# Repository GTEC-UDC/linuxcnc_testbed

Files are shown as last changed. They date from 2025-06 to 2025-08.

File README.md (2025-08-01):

# LinuxCNC Motor Control Testbed

A motor control testbed using the open-source [LinuxCNC](https://www.linuxcnc.org) platform integrated with the [Mesa Electronics](https://store.mesanet.com/) 7i96S and 7I77 interface cards and the [igus® dryve D1](https://www.igus.eu/product/D1) motor controllers.

This system was used to develop and validate the control system for [a large high-precision 3-axis gantry robot system](https://github.com/GTEC-UDC/linuxcnc_gantry_robot).

<div align="center">






</div>

<div align="center">
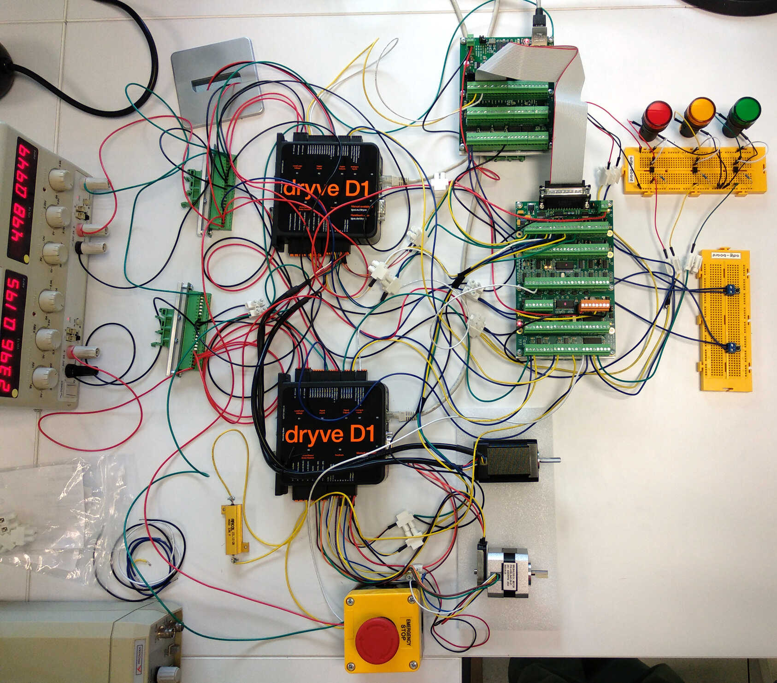
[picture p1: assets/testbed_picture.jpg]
LinuxCNC Motor Control Testbed Picture
  
</div>

<!-- Video uploaded via drag-and-drop to the GitHub editor -->
<!-- Note: GitHub does not render video files from the repository. See: https://github.com/orgs/community/discussions/19403 -->
<!-- The video is also stored at assets/testbed_video.webm within the repo -->
<video type="video/webm" src="https://github.com/user-attachments/assets/f6507526-396f-41c5-9737-cb749e45726b"><video/>

## Key Features

- **Real-time Control**: Precise real-time multi-axis motion using LinuxCNC with MESA interface cards and igus® dryve D1 motor controllers.
- **Dual Motor System**: Stepper and brushless motors.
- **Closed Loop Control**: High-precision encoder feedback for accurate positioning.
- **Safety Systems**: Emergency stop and limit switches.
- **Visual Indicators**: Custom LED status system.

## Documentation

- **Technical Documentation**: [Sphinx](https://www.sphinx-doc.org) documentation sources of the system documentation in [docs/](docs/). The documentation has been prepared to be built in HTML and PDF formats. To build the documentation follow the instructions below:

  1. **Prepare the environment**:

     ```bash
     cd docs
     uv venv && uv sync && source .venv/bin/activate
     ```

  2. **Build the documentation**:

     - HTML: `make html`

       The HTML documentation index file will be saved in `docs/build/html/index.html`.

     - PDF (requires a LaTeX installation with LuaLaTeX): `make latexpdf`

       The PDF file will be saved in `docs/build/latex/linuxcnc_motor_control_testbed.pdf`.

- **Electrical Schematics**: [KiCAD](https://www.kicad.org/) electrical schematics in [schematics/](schematics/).

## Hardware Components

| Component | Model | Quantity | Function |
|---|---|---|---|
| **Control Computer** | PC running [LinuxCNC](https://www.linuxcnc.org) | 1 | Real-time motor coordination |
| **Motor Controllers** | [igus® dryve D1](https://www.igus.eu/product/D1) | 2 | Individual motor control |
| **Main Interface** | [MESA 7I96S](https://store.mesanet.com/index.php?route=product/product&product_id=374) | 1 | Ethernet-LinuxCNC bridge. Stepper motor control. Limits detection |
| **I/O Expansion** | [MESA 7I77](https://store.mesanet.com/index.php?route=product/product&product_id=120) | 1 | Brushless motor control. Encoder inputs. Emergency stop detection and LED indicators|
| **Stepper Motor** | [STEPPERONLINE 17HS24-2104-ME1K](https://www.omc-stepperonline.com/nema-17-closed-loop-stepper-motor-65ncm-92oz-in-with-magnetic-encoder-1000ppr-4000cpr-17hs24-2104-me1k) | 1 | Stepper motor with 1000 PPR magnetic encoder |
| **Brushless Motor** | [STEPPERONLINE 42BLS40-24-01](https://www.omc-stepperonline.com/es/24v-4000rpm-0-0625nm-26w-1-8a-42x42x40mm-motor-cc-sin-escobillas-42bls40-24-01) + [CUI Devices AMT102-0512-I5000-S](https://mou.sr/3GkCI6g) | 1 | Brushless motor with 512 PPR optical encoder |
| **Power Supply** | [Aim-TTI EL302RD](https://www.aimtti.com/product-category/dc-power-supplies/aim-el-rseries) | 1 | Dual output (24V/5V) |
| **Emergency Stop** | Push-button with NO/NC contacts | 1 | System safety shutdown |
| **Limit Switches** | Push-button switches | 2 | Position boundary detection |
| **LED Indicators** | 24 V panel mount LEDs | 3 | System state indication |

## System Architecture

Prototype System

## Repository Structure

```txt
linuxcnc-testbed/
├── README.md      # This file
├── assets/        # Pictures and videos
├── docs/          # Technical Documentation
├── linuxcnc/      # LinuxCNC configurations
├── schematics/    # Wiring diagrams
├── scripts/       # Example control scripts
└── gcode/         # G-code example
```

## License

### General License (unless otherwise specified)

<a rel="license" href="http://creativecommons.org/licenses/by-sa/4.0/">

</a>

[LinuxCNC Motor Control Testbed](https://github.com/GTEC-UDC/linuxcnc_testbed) © 2025 by [Tomás Domínguez Bolaño](https://orcid.org/0000-0001-7470-0315), [Valentín Barral Vales](https://orcid.org/0000-0001-8750-7960), [Carlos José Escudero Cascón](https://orcid.org/0000-0002-3877-1332), and [José Antonio García Naya](https://orcid.org/0000-0002-1944-4678) (CITIC Research Center, University of A Coruña, Spain) is licensed under [Creative Commons Attribution-ShareAlike 4.0 International](https://creativecommons.org/licenses/by-sa/4.0/) (CC BY-SA 4.0). To view a copy of this license, see the [LICENSE-CC](LICENSE-CC) file or visit <https://creativecommons.org/licenses/by-sa/4.0/>.

### Documentation License ([docs/](docs/))

Copyright © 2000-2022 LinuxCNC.org\
Copyright © 2025 Tomás Domínguez Bolaño, Valentín Barral Vales, Carlos José Escudero Cascón, and José Antonio García Naya.

Permission is granted to copy, distribute and/or modify this document
under the terms of the GNU Free Documentation License, Version 1.3
or any later version published by the Free Software Foundation;
with no Invariant Sections, no Front-Cover Texts, and no Back-Cover Texts.
A copy of the license is included in the section entitled "GNU Free Documentation License".

## Acknowledgements

This work has been supported by grant PID2022-137099NB-C42 (MADDIE) and by project TED2021-130240B-I00 (IVRY) funded by MCIN/AEI/10.13039/501100011033 and the European Union NextGenerationEU/PRTR.

<div align="center">
  Acknowledgements logos
</div>

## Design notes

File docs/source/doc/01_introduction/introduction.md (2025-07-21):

# Introduction

The system uses LinuxCNC as its control platform, with two igus® dryve D1 controllers which are used to control a stepper motor and a brushless motor, respectively. The system diagram is shown in {numref}`fig:system_diagram`. Below, we detail the system's configuration, including the boards and components used.

:::{ext-figure} images/system_diagram.\*
:height-html: 300px
:name: fig:system_diagram

System diagram.
:::

## LinuxCNC

LinuxCNC, formerly known as the {{EMC}}, is a software system designed for the computer control of various machine tools, such as milling machines and lathes, as well as robots like PUMA and SCARA, and other computer-controlled machinery with up to nine axes. LinuxCNC is free, open-source software. Current versions are fully licensed under the [{{GPL}}](https://www.gnu.org/licenses/gpl.html) and [{{LGPL}}](https://gnu.org/licenses/lgpl.html).

In our system, LinuxCNC communicates with the igus® dryve D1 controllers via the MESA 7I96S and 7I77 boards. LinuxCNC is responsible for coordinating the operation of all motors, providing precise, real-time control over the system.

Detailed information on LinuxCNC’s operation and configuration can be found in {numref}`sec:linuxcnc`.

## System Hardware

{numref}`fig:installation` shows a photograph of the testbed setup. This system comprises the following key components:

:::{figure} images/installation_labelled.*
:name: fig:installation

Testbed setup.
:::

- **[Aim-TTI EL302RD](https://www.aimtti.com/product-category/dc-power-supplies/aim-el-rseries) Dual Power Supply**: Provides two independent power outputs, each capable of delivering a maximum of 30 V and 2 A. For the testbed setup, we required 24 V and 5 V power.

- **Two [igus® dryve D1](https://www.igus.eu/product/D1) Motor Controllers**: igus® dryve D1 can be used for controlling stepper, DC, and brushless motors in industrial and automation applications. The igus® dryve D1 supports the following communication methods with control systems:

  - **CANopen**: A communication protocol widely used in industrial automation systems, built upon the CAN bus (ISO 11898) standard.
  - **Modbus TCP**: A communication protocol extensively employed in industrial applications for data transmission over Ethernet networks using the TCP protocol.
  - **Analog and Digital Signals**: In addition to network communication options, the igus® dryve D1 can receive analog and digital signals for direct control.

    In this system, we communicate with the igus® dryve D1 controllers using MESA 7I96S and 7I77 boards using digital and analog signals. This setup enables LinuxCNC to have precise, real-time control over the motors' operation.

- **[MESA 7I96S](https://store.mesanet.com/index.php?route=product/product&product_id=374) Board**: This board is the primary hardware interface between LinuxCNC and the igus® dryve D1 controllers. It connects to the computer running LinuxCNC via an Ethernet connection. Its main functions include:

  - Controlling the stepper motor by sending step and direction signals to its designated igus® dryve D1 controller.
  - Receiving input signals from limit switches.

- **[MESA 7I77](https://store.mesanet.com/index.php?route=product/product&product_id=120) Daughter Board**: This board connects to the 7I96S board via a 25-pin flat cable. Its primary functions are:

  - Controlling the brushless motor by sending an analog speed signal to its corresponding igus® dryve D1 controller.
  - Receiving position feedback signals from motor encoders.
  - Receiving warning and error signals from the controllers.
  - Receiving the emergency stop signal when the emergency stop switch is activated.

- **Brushless Motor**: A [STEPPERONLINE 42BLS40-24-01](https://www.omc-stepperonline.com/24v-4000rpm-0-0625nm-26w-1-8a-42x42x40mm-brushless-dc-motor-42bls40-24-01), equipped with a [CUI Devices AMT102-0512-I5000-S](https://www.cuidevices.com/product/motion-and-control/rotary-encoders/incremental/modular/amt10-series) optical encoder of 512 {{PPR}}.

- **Stepper Motor**: A [STEPPERONLINE 17HS24-2104-ME1K](https://www.omc-stepperonline.com/nema-17-closed-loop-stepper-motor-65ncm-92oz-in-with-magnetic-encoder-1000ppr-4000cpr-17hs24-2104-me1k). This motor includes a 1000 {{PPR}} magnetic encoder.

- **LED Indicators**: Custom indicators with red, yellow, and green LEDs, which provide a visual display of the system's status.

- **Two Buttons for Limit Sensor Simulation**.

- **Emergency Stop Switch**: This switch has both a normally closed and a normally open contact.

The system wiring diagram, detailing all components and their interconnections, is available in the {{project_url_link}}.

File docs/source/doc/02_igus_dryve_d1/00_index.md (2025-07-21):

# igus® dryve D1 Controllers

:::{important}
For the testbed development we used the igus® dryve D1 controllers with firmware version `dryve-D1-1-20220525` and their operating manual with version `3.0.1`.
:::

In this section, we will detail the configuration of the igus® dryve D1 controllers. To configure them, connect each controller to a PC via an Ethernet cable. If you do not know a controller's IP address, you can find it by powering on the device or reconnecting the Ethernet cable. In either case, the controller will sequentially display its IP address, digit by digit, on the seven-segment display located on its front panel.

Once connected, open a web browser and enter the IP address of the controller you wish to configure. This will grant access to the controller's web-based configuration interface. The following sections describe the controller's configuration parameters and the values to be applied for both the brushless and stepper motors. For more comprehensive information, it is recommended to consult the official controller manual.

:::{toctree}
:maxdepth: 2
:caption: Table of Contents

01_start_page.md
02_motor_page.md
03_axis_page.md
04_communication_page.md
05_inputs_ouputs_page.md
06_drive_profile_page.md
07_oscilloscope_page.md
:::

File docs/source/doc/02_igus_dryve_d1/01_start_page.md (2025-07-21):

(sec:conf_start)=
# "Start" Page

The "Start" configuration page, shown in {numref}`fig:conf_stepper_1`, contains various general settings. Specifically, we will configure the following options for all the controllers:

- **Measuring system**: Metric, Millimeter
- **Movement type**: Rotary
- **Time units**: Seconds

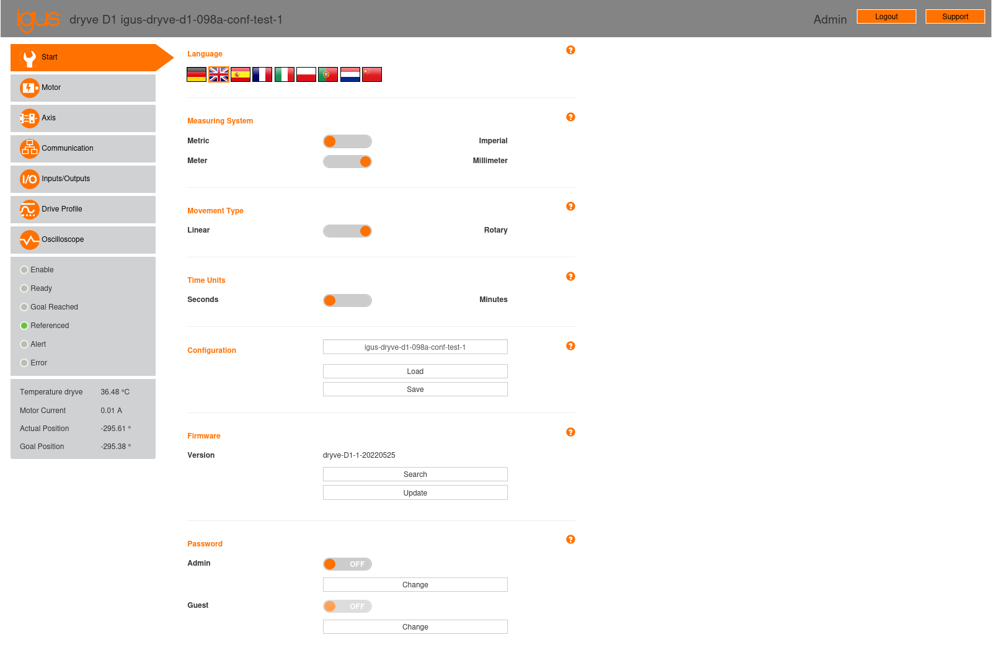
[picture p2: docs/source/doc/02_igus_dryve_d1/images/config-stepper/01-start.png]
:::{figure} images/config-stepper/01-start.png
:name: fig:conf_stepper_1

Initial configuration page of the stepper motor controller.
:::

:::{note}
We have configured the Movement type option as "Rotary," despite the motor driving a linear axis. This is because we do not require the controller to control the axis position, LinuxCNC will handle this. Our only requirement is for the controller to respond to the movement signals we transmit.
:::

Additionally, this page includes the following sections:

- **Configuration**: This section allows you to save the current controller configuration to a file and load a configuration from a file. Once the controller configuration is defined, it is recommended to use this functionality to save it.
- **Firmware**: This section enables updating the controller firmware. The "Search" button directs you to the URL for downloading the latest firmware version. The "Update" button allows you to load the firmware file from your disk to update the controller.
- **Password**: This section allows you to set a password for "Admin" and "Guest" users. These users can be activated or deactivated using their respective switches. If both users are deactivated (the default setting), the user interface is accessed with the "Admin" user. The "Guest" user can only be activated if the "Admin" user has been previously activated.

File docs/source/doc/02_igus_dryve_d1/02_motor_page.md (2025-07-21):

# "Motor" Page

The "Motor" configuration page is shown in {numref}`fig:conf_stepper_2`. Below, we describe the various available options and their appropriate settings.

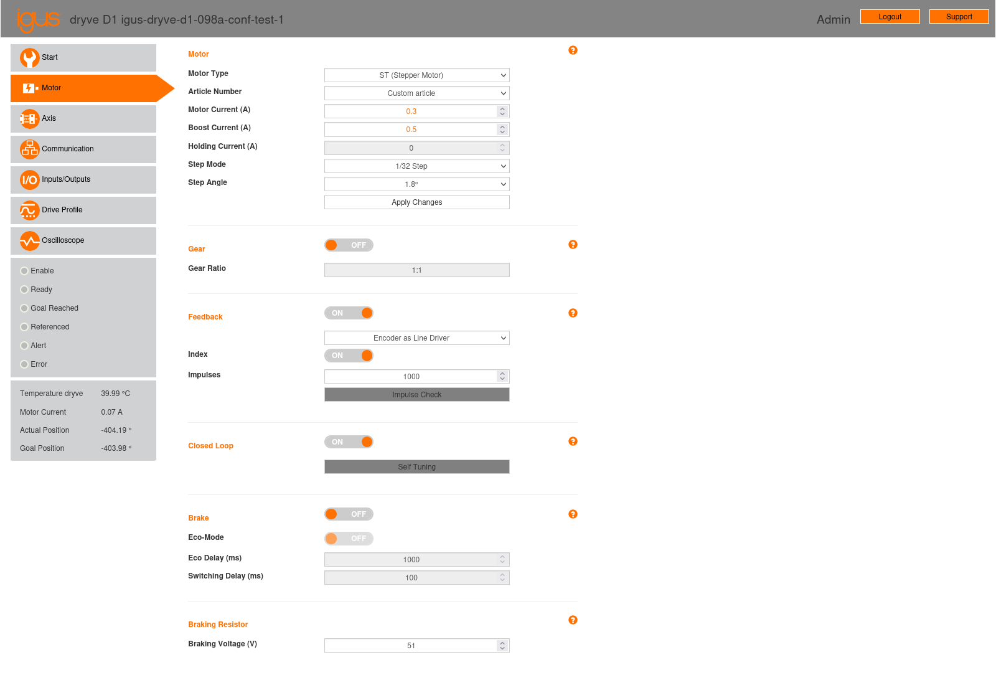
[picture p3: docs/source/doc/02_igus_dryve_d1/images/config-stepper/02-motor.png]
:::{figure} images/config-stepper/02-motor.png
:name: fig:conf_stepper_2

"Motor" configuration page of the stepper motor controller.
:::

(sec:motor_motor)=

## Motor

- **Motor Type**: The type of motor. For our application, select "EC/BLDC (Brush-Less DC Motor)" for the brushless motor and "ST (Stepper Motor)" for the stepper motor.

- **Article Number**: For igus® motors, you can select the motor's article number. In that case, parameters such as "Motor Current," "Boost Current," "Holding Current," "Step Angle," and "Pole pairs," along with other settings in the "Gear," "Feedback," "Closed Loop," "Brake," and "Braking Resistor" sections, will be automatically populated with default values corresponding to the selected motor model.

    In our testbed setup, we opted for "Custom article" since we are using different motors.

- **Motor Current (A)**: Defines the maximum permissible continuous current for the motor during sustained movements, i.e.,excluding acceleration and deceleration phases (refer to the "Boost Current" option for those cases). Values can range from 0 A to 7 A.

    :::{important}
    This parameter must be less than the maximum current that the power supply can provide, also considering any other loads it must supply power to.
    :::

    In the testbed setup, as both motors are small, have no load to move, and the power supply delivers a maximum of 2A, we have set small values for this parameter: 0.3 A for the stepper motor and 1 A for the brushless motor.

- **Boost Current (A)**: Defines the maximum permissible current for the motor during acceleration and deceleration phases. During these periods, the maximum motor current set in the "Motor Current" parameter can temporarily increase up to the boost current value for a maximum duration of 2 seconds. Possible values range from the "Motor Current" parameter value up to 150 % (for stepper motors) or 300 % (for brushless motors) of the "Motor Current" parameter value.

    :::{important}
    As with the previous parameter, this value must be less than the maximum current the power supply can provide, taking into account any additional loads.
    :::

    In the testbed setup, as with the previous parameter, we have set small values for this parameter: 0.5 A for the stepper motor and 1 A for the brushless motor.

- **Holding Current (A)**: Defines the current supplied to the motor when it is stopped. This setting is applicable only to open-loop stepper motors, otherwise the parameter will be disabled and grayed out.

    In our testbed setup, the controller was configured for closed-loop operation, so this option is disabled.

- **Step Mode**: This setting is applicable only to stepper motors, otherwise it will be disabled and grayed out. This parameter defines the microstepping technique to control the motor {cite}`electricmotorsanddrives,enwiki:1166298756`. Instead of moving the motor one full step at a time (1/1 step mode), microstepping divides each step into smaller fractions, enabling a greater number of intermediate positions. Available modes include "Auto," 1/1 (full step), 1/2, 1/4, 1/8, 1/16, 1/32, and 1/64.

    Smaller step sizes result in more precise positioning, improved movement stability, and reduced noise emission. However, the theoretical maximum speed will decrease. For example, a motor with a 1.8° step angle requires 200 steps to complete one revolution in 1/1 step mode. Generally, for a step angle $\theta$ and 1/N step mode, $360N/\theta$ steps are needed per revolution. Given that the controller can process step pulses with a minimum pulse period $T$, the theoretical maximum motor speed in RPM will be $60\theta/(360NT) = \theta/(6NT)$. Therefore, for a 1/N step mode, the theoretical maximum speed will be reduced by a factor of N compared to the theoretical maximum speed of the 1/1 mode.

    The igus® dryve D1 documentation specifies a minimum step pulse period of 40 μs. However, the actual minimum period is smaller. Using a signal generator and an oscilloscope, we have verified that the actual minimum step pulse period supported by the igus® dryve D1 is 4 μs. {numref}`tab:step_modes` shows the steps per revolution and theoretical maximum speeds in RPM for each step mode, considering a 1.8° step angle and a 4 μs minimum step pulse period. Note that the speeds presented in the table are theoretical values calculated from the formula $\theta/(6NT)$. In practice, stepper motors are not designed to reach high speeds. The maximum speed of a stepper motor depends on the motor model, but typically these motors do not exceed 1000 RPM.

    In our testbed setup, we have set the step mode to 1/32.

  :::{csv-table} Step modes, steps per revolution, and theoretical maximum speeds in rpm, considering a step angle of 1.8° and a minimum step pulse period of 4 µs.
  :class: align-col1-r, align-col2-r, align-col3-r
  :name: tab:step_modes
  :header: Step Mode, Steps per revolution, Maximum speed (rpm)
  :widths: auto

  1, 200, 75000
  1/2, 400, 37500
  1/4, 800, 18750
  1/8, 1600, 9370
  1/16, 3200, 4680
  1/32, 6400, 2340
  1/64, 12800, 1170
  :::

- **Step Angle**: This parameter, available only for stepper motors, defines the angle of a full motor step (e.g., 0.72°, 0.9°, 1.8°). It is a physical property of the motor itself and determines the number of full steps per revolution. For instance, a motor with a 1.8° step angle needs $360/1.8 = 200$ full steps per revolution.

    In our testbed setup, the stepper motor used has a step angle of 1.8°.

- **Pole Pairs**: This parameter, available only for brushless motors, defines the number and arrangement of the motor coils. It is a physical property of the motor itself.

    In our testbed setup, the brushless motor used has 4 pole pairs.

After completing the fields in this section, click the "Apply Changes" button.

## Gear

If the motor includes a reduction gear, it can be configured in this section. We will set this option to "OFF."

## Feedback

This section allows you to configure the parameters of the encoder connected to the controller. If an igus® motor was selected in the "Article Number" parameter within the "Motor" section, the parameters in this section will already be set to their correct values.

In our testbed setup, we have configured the following values, based on the specifications of the respective encoders:

- **Stepper motor**
  - **Type**: Encoder as a Line Driver
  - **Index**: ON
  - **Impulses**: 1000
- **Brushless motor**
  - **Type**: Encoder as Single Ended
  - **Index**: ON
  - **Impulses**: 512

:::{important}
The "Impulse Check" button prompts the controller to automatically verify the number of encoder impulses. To do this, it rotates the motor by one revolution, even if the "enable" signal is not activated. Therefore, do not to click this button if the motor cannot rotate freely.
:::

## Closed Loop

Through closed-loop control, the controller continuously compares the position information received from the encoder with the desired reference value and adjusts the motor based on this comparison. This continuous feedback enables error correction, maintaining the motor's desired position, speed, or state, and more efficiently adapting to load variations. This results in precise and stable motor control, significantly reducing energy consumption and operating temperature.

We will set this option to "ON."

:::{important}
For closed-loop control, the igus® dryve D1 internally uses two {{PI}} controllers to control current and speed, respectively, and a {{P}} controller for position control. The parameters of these controllers are shown on the "Oscilloscope" page (see {numref}`sec:oscilloscope_parameters`). If the "Self Tuning" button in this section is pressed, the controller will attempt to automatically determine the optimal values for these parameters.
:::

## Brake

The igus® dryve D1 can control a holding brake. Since none of our motors are equipped with a brake, we will set this option to "OFF."

## Braking Resistor

This section applies only to brushless motors. When decelerating, these motors act as power generators. This can produce voltage peaks that exceed the applied load voltage, potentially damaging the controller, especially during rapid decelerations. To prevent damage, a braking resistor must be used to dissipate the excess energy generated. Therefore, it is essential that each controller driving a brushless motor is equipped with its own braking resistor.

Both the resistor's value and its power dissipation capacity depend on the specific motor used. The controller manual provides detailed instructions on how to derive these values from the motor's data. In our testbed setup, we used a 33 Ω resistor with a maximum power dissipation of 50 W at 25 °C (with a standard heatsink) or 14 W (without a heatsink).

This section provides a single parameter, "Braking Voltage (V)," which sets the voltage threshold at which the braking resistor engages to dissipate excess energy. For safe operation, the controller incorporates a hysteresis of 1 V; thus, the braking resistor will activate when the motor voltage reaches the threshold voltage plus 1 V, and will deactivate when it drops to the threshold voltage minus 1 V.

The voltage threshold set in the "Braking Voltage" parameter should be slightly higher than the motor's supply voltage. For instance, if the motor's supply voltage is 24 V, a suitable threshold could be 26 V. If the motor's supply voltage is 48 V, a suitable threshold could be 51 V. A value set too high could result in insufficient energy dissipation and trigger the "E09 Load Supply High" error (refer to the controller manual, Section 7: Alerts and Errors).

In our testbed setup, the brushless motor was powered at 24 V, so we set this parameter to 26 V.

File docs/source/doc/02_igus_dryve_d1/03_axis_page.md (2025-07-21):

(sec:page_axis)=
# "Axis" Page 

The "Axis" configuration page is shown in {numref}`fig:conf_stepper_3`. As shown, the parameters use the units established on the initial configuration page (see {numref}`sec:conf_start`); thus, position parameters are in degrees (°), speed parameters in degrees per second (°/s), and acceleration parameters in degrees per second squared (°/s^2^). The various options available on this page and their recommended settings are described below.

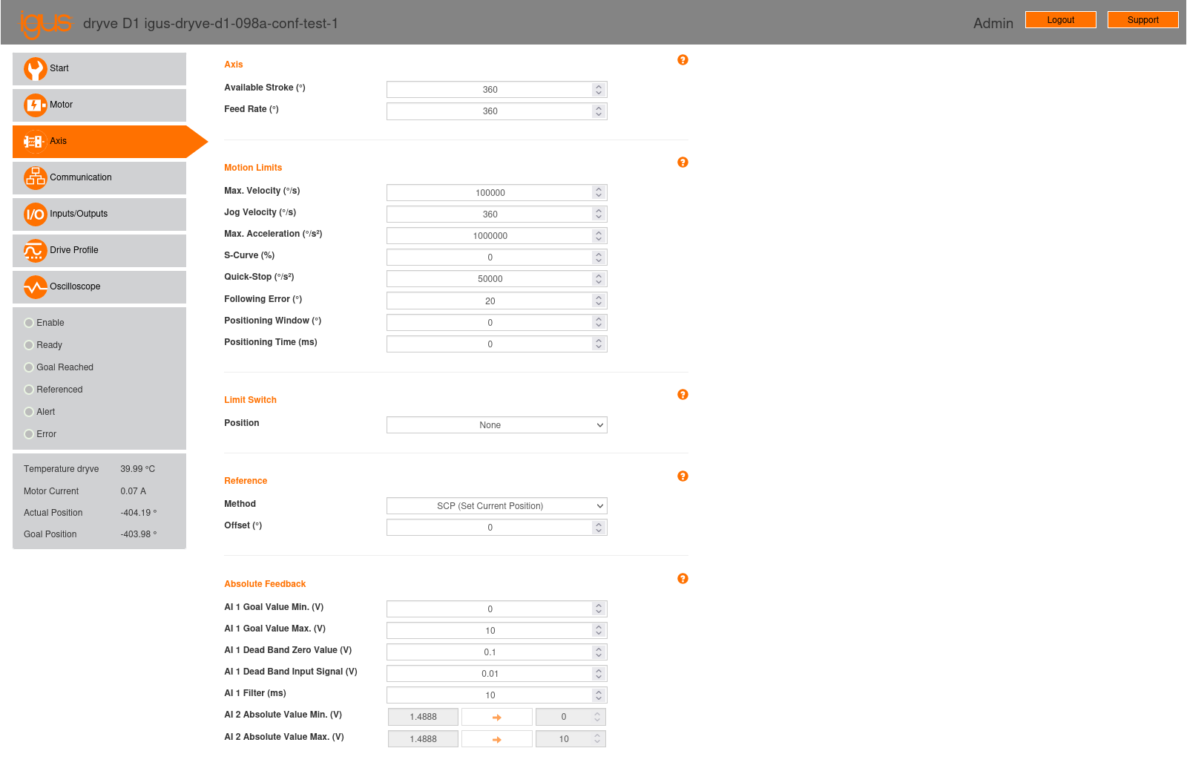
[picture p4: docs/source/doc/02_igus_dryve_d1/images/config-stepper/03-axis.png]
:::{figure} images/config-stepper/03-axis.png
:name: fig:conf_stepper_3

"Axis" configuration page of the stepper motor controller.
:::

## Axis

This section contains the following parameters:

- **Available Stroke**: Defines the movement range for the "ABS" (Absolute Positioning) mode. Since we will not be using this mode, this parameter is not relevant to our application.
- **Feed Rate**: For linear axes, this parameter indicates the axis displacement per motor rotation. As we are considering a rotary axis, we must set this parameter to 360°, as specified in Section 5.5.1 of the controller manual.

(sec:axis_motion_limits)=
## Motion Limits 

This section includes the following parameters:

- **Max. Velocity (°/s)**: This sets the maximum motor speed. It functions as a limit for the movement programming modes available on the "Drive Profile" page (see {numref}`sec:page_drive_profile`). For the stepper motor, speed will be controlled by the step signal received by the controller, so we want this parameter to be as high as possible. For the brushless motor, the maximum speed will be set on the "Drive Profile" page, with a value not exceeding that set here. Therefore, we will set this parameter to its maximum value: 100000 °/s.

- **Jog Velocity (°/s)**: This parameter defines the motor speed for manual positioning, accessible on the "Drive Profile" page (see {numref}`sec:page_drive_profile`). It is primarily useful for testing purposes via the controller's web interface; in our case, we have set it to 360 °/s. For the final system, this parameter is irrelevant.

- **Max. Acceleration (°/s{sup}`2`)**: This sets the maximum motor acceleration, used in manual positioning on the "Drive Profile" page (see {numref}`sec:page_drive_profile`). It also serves as a limit in the movement programming modes available on the "Drive Profile" page. Similar to speed, for the stepper motor, acceleration will be controlled by the step signal received by the controller. For the brushless motor, the maximum acceleration will also be set on the "Drive Profile" page, with a value not exceeding that set here. Therefore, we will set this parameter to its maximum value: 1000000 °/s{sup}`2`.

- **S-Curve (%)**: This parameter allows control over the rate of change of acceleration, known as "jerk" {cite}`enwiki:1178778094`. It can be adjusted between 0% and 100% to control the smoothness of acceleration and deceleration transitions in motor movement. Lower values will result in abrupt changes in acceleration, leading to higher "jerk" levels and, consequently, less smooth movements that can induce unwanted vibrations and stress on the system. Conversely, higher values will reduce "jerk," resulting in smoother acceleration and deceleration transitions, thereby minimizing vibrations and wear on both the motor and machinery.

    If an external controller (such as LinuxCNC) is to have full control over motor movement, this parameter should be set to 0%. In this configuration, any acceleration and deceleration smoothing within the motor controller itself is deactivated, allowing the external controller to directly manage the movement.

    However, LinuxCNC's current motion controller does not have a "jerk" limitation and uses constant acceleration. It might be desirable to set this parameter to a value greater than 0% to limit "jerk" and prevent unwanted vibrations and stress on the system. However, this approach would increase tracking error within LinuxCNC. Therefore, if this option is to be set above 0%, a balance between movement smoothness and tracking precision must be found.

    In our case, we have set the parameter to 0%.

- **Quick-Stop (°/s{sup}`2`)**: This specifies the deceleration rate when a movement stops in an emergency. A quick stop is executed if the controller's "Enable" signal (digital input X2.7) is revoked.

    :::{important}
    It is important to ensure that the specified deceleration is appropriate for the intended application. A deceleration that is too low could result in an excessive stop time for the robot's movement; conversely, a deceleration that is too high could damage the robot's mechanical structure.
    :::

    In our testbed setup, we have set this parameter to 50000 °/s{sup}`2`.

- **Following Error (°)**: This defines the permissible deviation of the actual position from the desired position. A warning is issued if 50% of the allowed tracking error is reached. If the allowed tracking error is exceeded, the movement stops, and an error is reported.

    In our testbed setup, we have set this parameter to 20°.

- **Positioning Window (°)**: This parameter defines a position range around a target point, extending in both positive and negative directions. For example, if the goal is to reach 100 mm and a positioning window of 10 mm is set, the system will consider the position to be within the target range if it falls anywhere between 90 mm and 110 mm. If the motor's actual position is within this window, the movement is considered complete, even if the motor is mechanically blocked. This prevents the system from continuously attempting to reach an exact position in case of an obstruction. If the positioning window is set to 0, this function is deactivated, and the system will not consider a range around the target point.

    In our testbed setup, we have set this parameter to 0, thereby deactivating this function.

- **Positioning Time (ms)**: This defines the duration, in milliseconds, for which the actual position must be maintained within the range defined by the positioning window before a movement is considered complete.

    In our testbed setup, we have set this parameter to 0.

(sec:limit_switch)=
## Limit Switch 

This section includes a "Position" parameter that allows for specifying the position and number of limit sensors used.

In our testbed setup, the limit sensors are not connected to the controllers, they are only connected to the MESA 7I96S board, so limits are entirely managed by LinuxCNC. Therefore, we set the "Position" parameter to "None."

## Reference

This section allows for selecting the preferred referencing ("homing") method and position displacement ("offset").

Similar to robot movement limits (see {numref}`sec:limit_switch`), the "homing" process will also be fully controlled by LinuxCNC. Therefore, we have set the following parameters:

- **Method**: SCP (Set Current Position)
- **Offset (°)**: 0

(sec:axis_absolute_feedback)=
## Absolute Feedback 

The igus® dryve D1 controller has two analog inputs, AI 1 (Analog Input 1, input X4.1) and AI 2 (Analog Input 2, input X4.2). These are used to configure and control the target position or speed and the current position of the system, respectively. In our system, we will use analog input AI 1 to control the brushless motor's speed; analog input AI 2 will not be used. For the stepper motor, these inputs are not applicable, making this section relevant only for the brushless motor. Below are the parameters related to the analog inputs available in this section.

- **Parameters related to AI 1 (input X4.1)**:

    The AI 1 input will be used to control the brushless motor's speed (see {numref}`sec:page_drive_profile`). The analog input control voltage will be ± 10 V, which must be configured on the "Inputs/Outputs" page (see {numref}`sec:page_input_outputs`). This voltage range must be considered when setting the AI 1 related parameters detailed below.

  - **AI 1 Target Value Min. (V)**: The minimum voltage value at analog input AI 1. We set its value to -10 V.
  - **AI 1 Target Value Max. (V)**: The maximum voltage value at analog input AI 1. We set its value to 10 V.
  - **AI 1 Dead Band Zero Value (V)**: This allows for setting a dead band symmetrically around 0 V in the target signal corresponding to analog input AI 1. This parameter can be specified in increments of 0.001 V. We set its value to 0 V.
  - **AI 1 Dead Band Input Signal (V)**: This allows for setting a dead band symmetrically around 0 V in the input signal of Analog Input AI 1. This parameter can be specified in increments of 0.001 V. We set its value to 0 V.
  - **AI 1 Filter (ms)**: This is the interval for averaging the signal. It is used to filter sudden signal variations and prevent inconsistencies in movement. Lower values result in a system that responds quickly but is more susceptible to noise or interference. Higher values result in a more stable system but with a longer response time. We set its value to 10 ms.

    The dead band parameters, "AI 1 Dead Band Zero Value" and "AI 1 Dead Band Input Signal," can be used to minimize unwanted motor movements during the idle state caused by increased ripple in the input signal or other interferences. Considering the above parameters, if the analog input voltage $x$ is already filtered as specified in the "AI 1 Filter" parameter, the target position or speed will be calculated using the following transfer functions:

  - $f_{\text{ZV}}(\cdot)$, corresponding to the "AI 1 Dead Band Zero Value" parameter and shown in {numref}`fig:deadband_zv`.
  - $f_{\text{IS}}(\cdot)$, corresponding to the "AI 1 Dead Band Input Signal" parameter and shown in {numref}`fig:deadband_is`.

    Thus, for the analog input value $x$, the target position or speed will be:

    $$y = (f_{\text{ZV}} \circ f_{\text{IS}})(x) = f_{\text{ZV}}(f_{\text{IS}}(x))$$

    :::{note}
    The calculation of the target position or speed is not explicitly stated in the controller manual (considering manual version 3.0.1) and has been determined experimentally. The manual only textually describes the "AI 1 Dead Band Zero Value" and "AI 1 Dead Band Input Signal" parameters, similar to the descriptions provided above.
    :::

:::{figure} images/f_zv/fig.*
:name: fig:deadband_zv

Transfer function $f_{\text{ZV}}(\cdot)$.
:::

:::{figure} images/f_is/fig.*
:name: fig:deadband_is

Transfer function $f_{\text{IS}}(\cdot)$.
:::

- **Parameters related to AI 2 (input X4.2)**:

    Analog input AI 2 is used to provide position information to the controller via an analog signal. In our case, we will not be using this input, so the parameters related to it are irrelevant.

  - **AI 2 Absolute Value Min (V)**: The minimum voltage value at analog input AI 2.
  - **AI 2 Absolute Value Max (V)**: The maximum voltage value at analog input AI 2.

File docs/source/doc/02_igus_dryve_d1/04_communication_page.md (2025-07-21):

(sec:page_communication)=
# "Communication" Page 

The "Communication" configuration page, shown in {numref}`fig:conf_stepper_4`, allows for the configuration of Ethernet and the controller's bus systems. Below we describe the various options available on this page and their recommended settings.

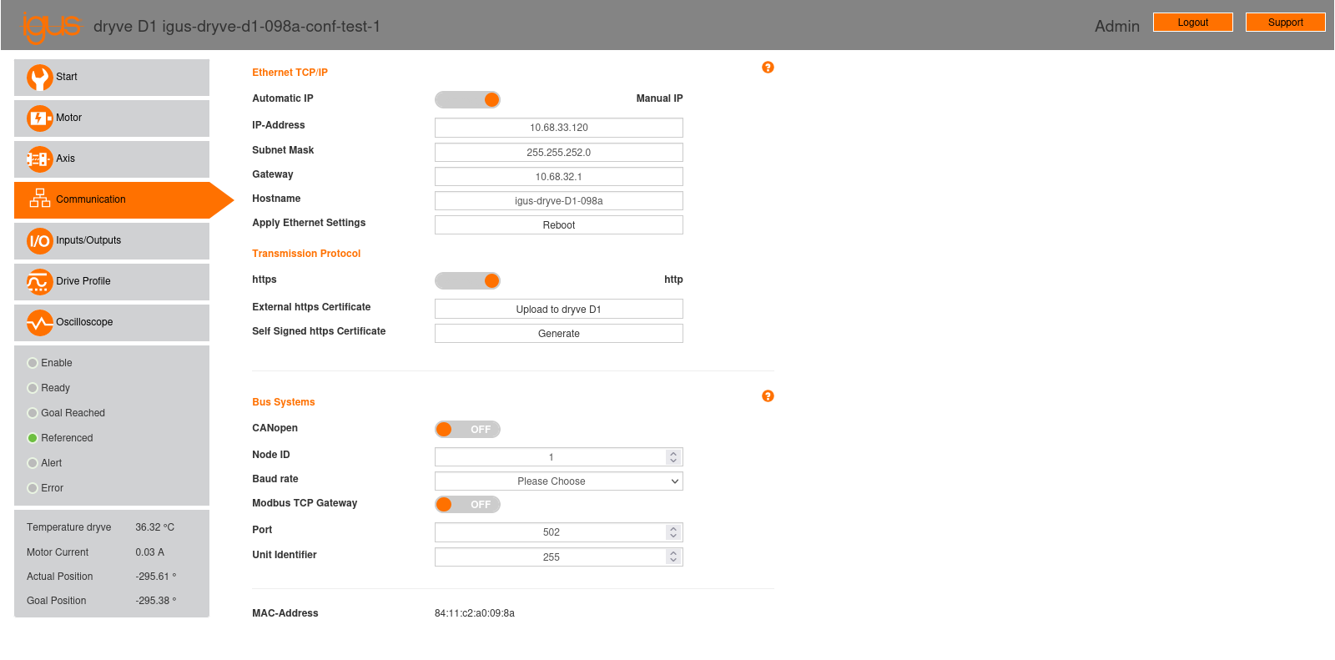
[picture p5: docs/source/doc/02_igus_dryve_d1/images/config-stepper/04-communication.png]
:::{figure} images/config-stepper/04-communication.png
:name: fig:conf_stepper_4

"Communication" configuration page of the stepper motor controller.
:::

## Ethernet TCP/IP

This section allows for configuring TCP/IP connection parameters: IP address, subnet mask, gateway, and hostname. After setting these parameters, you must click the "Reload" button to apply the changes.

In our testbed setup, these parameters were manually configured to the values shown in {numref}`tab:conf_ethernet`. The controllers were connected to a laptop PC via a switch. The parameters were configured to enable connectivity to the laboratory network, although this connection was not ultimately established.

:::{csv-table} Ethernet configuration parameters.
:name: tab:conf_ethernet
:widths: auto
:header: Parameter,Stepper motor,Brushless motor

IP-Address,  10.68.33.120,       10.68.33.121
Subnet Mask, 255.255.252.0,      255.255.252.0
Gateway,     10.68.32.1,         10.68.32.1
Hostname,    igus-dryve-D1-098a, igus-dryve-D1-098e
:::

## Transmission Protocol

This section allows you to select whether communication with the dryve D1 controller's web server should be via an unencrypted HTTP connection or an encrypted HTTPS connection. For an HTTPS connection, an external certificate can be provided, or a self-signed certificate can be generated.

In our testbed setup, the option to use an unencrypted HTTP connection was selected.

## Bus Systems

The controller is equipped with two bus systems, CANopen and Modbus, which enable communication with the controller and control of motor movement. In our case, we will not use either of these systems, as we will control the motor using the inputs and outputs of connectors X2 (digital inputs), X3 (digital outputs), and X4 (analog inputs). Therefore, the "CANopen" and "Modbus TCP Gateway" options have been left at their default setting of "OFF."

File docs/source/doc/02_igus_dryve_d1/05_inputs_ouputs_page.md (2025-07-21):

(sec:page_input_outputs)=
# "Inputs/Outputs" Page 

The "Inputs/Outputs" configuration page, displayed in {numref}`fig:conf_stepper_5`, allows for configuring the controller's inputs and outputs.

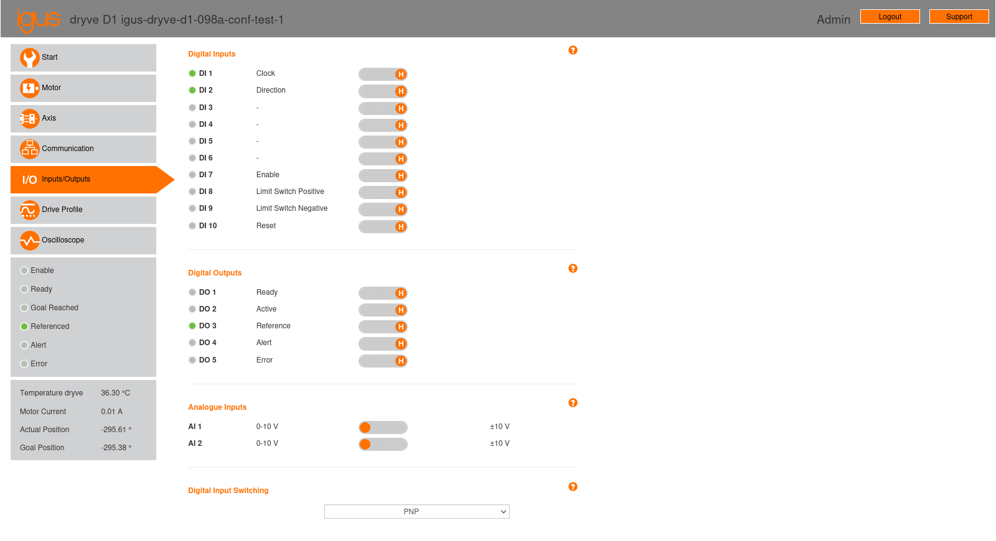
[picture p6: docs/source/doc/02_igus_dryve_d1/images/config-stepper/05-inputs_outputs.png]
:::{figure} images/config-stepper/05-inputs_outputs.png
:name: fig:conf_stepper_5

"Inputs/Outputs" configuration page of the stepper motor controller.
:::

The digital logic level used by the controller is set by supplying input X2.11 with a voltage between 5 V and 24 V. The controller's digital logic operates as follows:

- Digital outputs are set to 0 V for a low level (L) and to the voltage of X2.11 for a high level (H).
- Digital inputs will be evaluated as a low level (L) for voltages between 0% and 10% of the X2.11 voltage, and as a high level (H) for values exceeding 60% of the X2.11 voltage.

These levels are illustrated in {numref}`fig:controller_logic_levels`.

:::{figure} images/logic_levels/fig.*
:name: fig:controller_logic_levels

Controller digital logic levels.
:::

To interact with the controller's digital inputs and outputs, we use the MESA 7I96S and 7I77 boards:

- The MESA 7I96S board transmits step and direction signals to the stepper motor controller; these signals operate on 5 V logic.
- The MESA 7I77 board sends "start" and "enable" signals, and reads the "ready," "alert," and "error" outputs from the controllers (refer to the wiring diagram in the {{project_url_link}}. The logic voltage for the MESA 7I77 board can be adjusted by supplying input TB2.1 ("field power") with the desired voltage, ranging from 5 V to 28 V.

Because the MESA 7I96S board can only use 5 V logic for step and direction signals, we have set the logic voltage for both the igus® dryve D1 controllers (X2.11 input) and the MESA 7I77 board (TB2.1 input) to 5 V.

The sections available on this page are:

- **Digital Inputs**: This section shows the digital inputs and allows you to select between normally open (H) or normally closed (L) for each. Normally open (H) inputs will activate upon receiving a high signal. Conversely, normally closed (L) inputs will activate upon receiving a low signal. We will keep all inputs set to their default value (H).

    :::{note}
    The labels for the digital inputs shown on this page will vary depending on the motor control mode selected on the "Drive Profile" page (see {numref}`sec:page_drive_profile`). {numref}`fig:conf_stepper_5` shows the configuration for the stepper motor, which includes inputs for the "step/direction" control mode.
    :::

- **Digital Outputs**: This section shows the digital outputs and allows you to select between normally open (H) or normally closed (L) for each. We will keep all outputs set to their default value (H).

- **Analog Inputs**: This section shows the analog inputs and allows you to set the supported value range from 0 V to 10 V or from -10 V to 10 V. In our case, we will use analog input AI 1 with -10 V to 10 V signals to control the speed of the brushless motor, as mentioned in {numref}`sec:axis_absolute_feedback`. Therefore, on the brushless motor controller, we will set the AI 1 option to ± 10 VDC. We will leave the AI 2 option unchanged, as we will not be using that input.

- **Digital Input Switching**: This parameter determines how the system interprets digital input signals. The available options are PNP and NPN:

  - **PNP** (sourcing): In the activated state, the input is raised to the voltage applied at X2.11. In the deactivated state, the input is grounded via a pull-down resistor. In this configuration, current flows from the output of the higher-level control system to the input of the igus® dryve D1.
  - **NPN** (sinking): In the activated state, the input is grounded. In the deactivated state, the input is raised to the voltage applied at X2.11 due to a pull-up resistor. In this configuration, current flows from the input of the igus® dryve D1 to the output of the higher-level control system.

    Since all inputs and outputs of the MESA boards are of the PNP (sourcing) type, we will leave this option set to the default value "PNP."

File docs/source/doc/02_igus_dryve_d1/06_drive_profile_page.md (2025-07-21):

(sec:page_drive_profile)=
# "Drive Profile" Page 

This page allows you to select the control mode for executing movements. The available modes are:

- **Binary**: Movement control using digital or analog inputs and digital outputs.
- **Tipp/Teach**: Movement control using digital or analog inputs and digital outputs. In this mode, it is possible to modify the target positions of existing movements using digital inputs.
- **Step/Direction**: Movement control based on step and direction signals. This mode is only available for stepper motors.
- **CANopen**: Movement control via the CANopen communication protocol.
- **Modbus TCP**: Movement control via the Modbus TCP communication protocol.

Next, we will describe the configurations to apply to the motors.

## Stepper motor

For the stepper motor, we select the "step/direction" control mode. {numref}`fig:conf_stepper_6` shows the "Drive Profile" configuration page for the stepper motor controller when using the "step/direction" control mode. This control mode does not require any additional configuration; the page will simply show usage information for the step and direction signals.

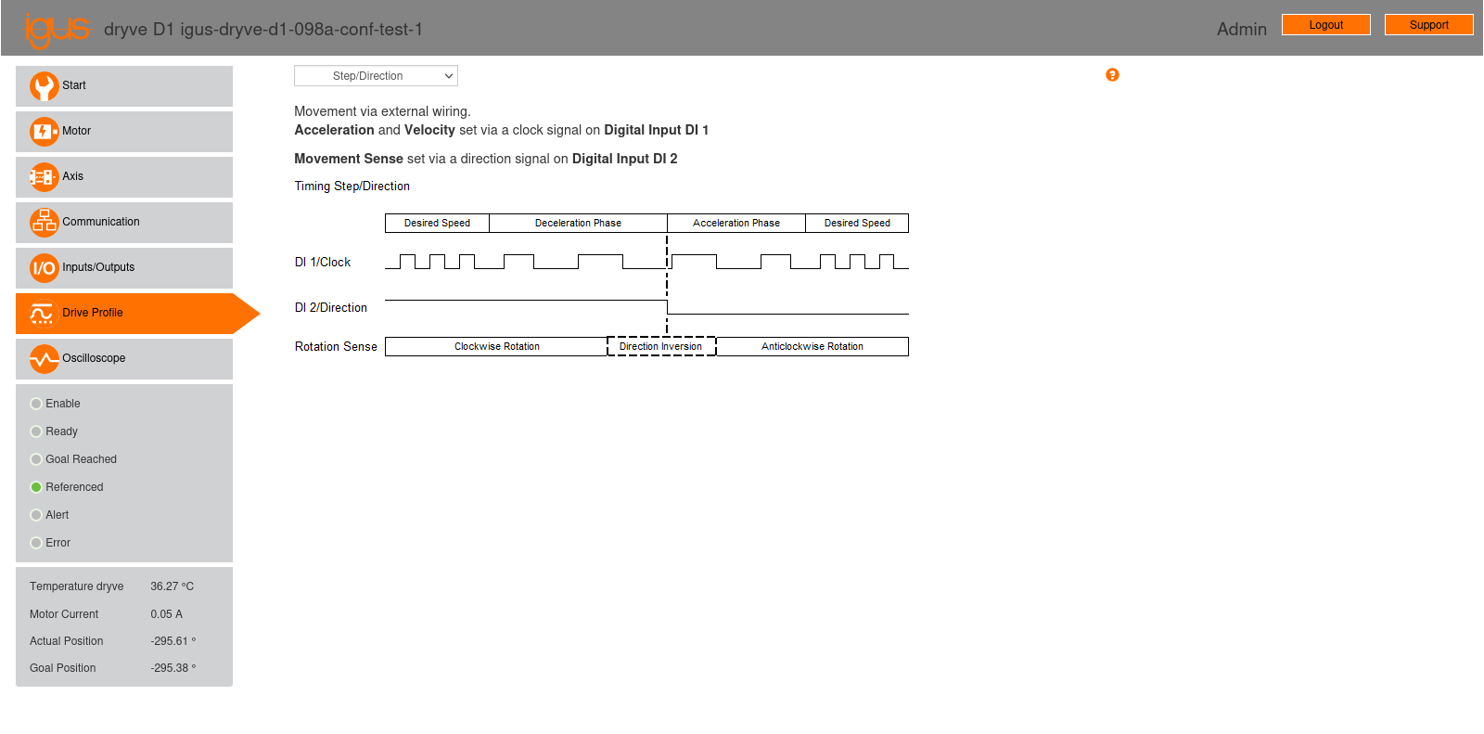
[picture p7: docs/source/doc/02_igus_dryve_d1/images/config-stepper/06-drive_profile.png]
:::{figure} images/config-stepper/06-drive_profile.png
:name: fig:conf_stepper_6

"Drive Profile" configuration page of the stepper motor controller, using the "step/direction" control mode.
:::

## Brushless motor

For the brushless motor, we select the "binary" control mode. {numref}`fig:conf_brushless_6` shows the "Drive Profile" configuration page for the brushless motor controller, using the "binary" control mode. This mode provides a movement table (see {numref}`fig:conf_brushless_6`) that allows for programming up to 32 parameterized movements, specifying the movement mode, target, maximum acceleration, speed, and the number of the next movement to execute. For the brushless motor, we will enter a single movement at position 1 using ADR (Analogue Rotation with Direction Definition) mode. ADR mode enables rotary movements by setting their speed via analog input AI 1.

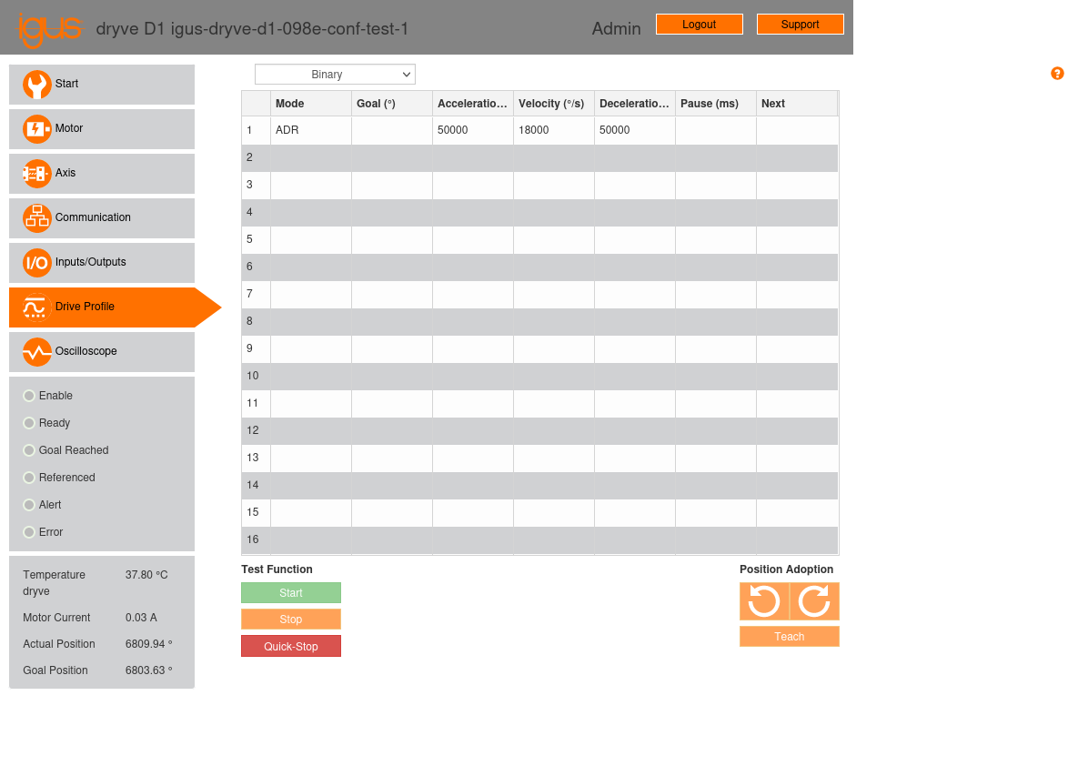
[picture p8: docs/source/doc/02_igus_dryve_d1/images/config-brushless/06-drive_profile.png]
:::{figure} images/config-brushless/06-drive_profile.png
:name: fig:conf_brushless_6

"Drive Profile" configuration page of the brushless motor controller, using the "binary" control mode.
:::

In our testbed setup, we have configured the following parameters for the movement at position 1:

- **Mode**: ADR (Analogue Rotation with Direction Definition).
- **Goal (°)**: This field will be left empty.
- **Acceleration (°/s{sup}`2`)**: 50000 °/s{sup}`2`, which is equivalent to 138.89 rev/s{sup}`2`.
- **Velocity (°/s)**: 18000 °/s, which is equivalent to 3000 rpm.
- **Deceleration (°/s{sup}`2`)**: 50000 °/s{sup}`2`, identical to the acceleration setting.
- **Pause (ms)**: This field will be left empty.
- **Next**: This field will be left empty.

As explained in {numref}`sec:page_input_outputs`, analog input AI 1 was configured to operate within a range of ±10 V. The controller will vary the motor speed proportionally to the applied analog signal. Thus, when input AI 1 is set to -10 V, the motor will rotate at 3000 rpm counter-clockwise, while when adjusted to 10 V, the motor will rotate at 3000 rpm clockwise.

Once the movement is configured, it must be activated for the controller to move the motor. There are two activation methods:

1. Select the movement by clicking on row number 1 of the movement table and then clicking the "start" button at the bottom of the page.
2. Use the controller's digital inputs and outputs.

While option 1 may be suitable for testing, implementing option 2 is necessary for a production system. In this scenario, for a powered controller with the "enable" signal not yet activated, the following steps should be followed:

1. Set digital inputs 1 to 5 (X2.1 to X2.5) with the selected movement number minus one, where input 1 represents the least significant bit and input 5 the most significant. For example, for movement number 1, the inputs will be set to 00000; for 2, to 00001; and so on, up to 32, which will be set to 11111. For movement number 1, which is our case, digital inputs 1 to 5 can simply be left disconnected.
2. Set digital input 7 (X2.7, the "enable" input) to a high level.
3. Once the "enable" input is activated, wait for the controller to set digital output 1 (X3.1, the "ready" output) to a high level. This output indicates that the controller is prepared to accept position commands.
4. Once the "ready" output is activated, send a square pulse to digital input 6 (X2.6, the "start" signal) to initialize the movement program. The controller has a debounce filter with a time of 10 ms on digital inputs 1 to 10 (excluding step and direction inputs), so the pulse must have a duration greater than 10 ms for the controller to detect it. In our testbed setup, we have set the pulse duration to 100 ms.

In our testbed setup, the movement activation process has been configured in LinuxCNC and is executed using the MESA 7I77 board, which sends and receives the corresponding signals.

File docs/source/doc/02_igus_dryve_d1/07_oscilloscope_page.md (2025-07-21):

(sec:page_oscilloscope)=
# "Oscilloscope" Page 

The "Oscilloscope" page, shown in {numref}`fig:conf_brushless_7`, offers two essential functionalities for adjusting and monitoring motor performance: the internal oscilloscope and the configuration of the motor's closed-loop control parameters.

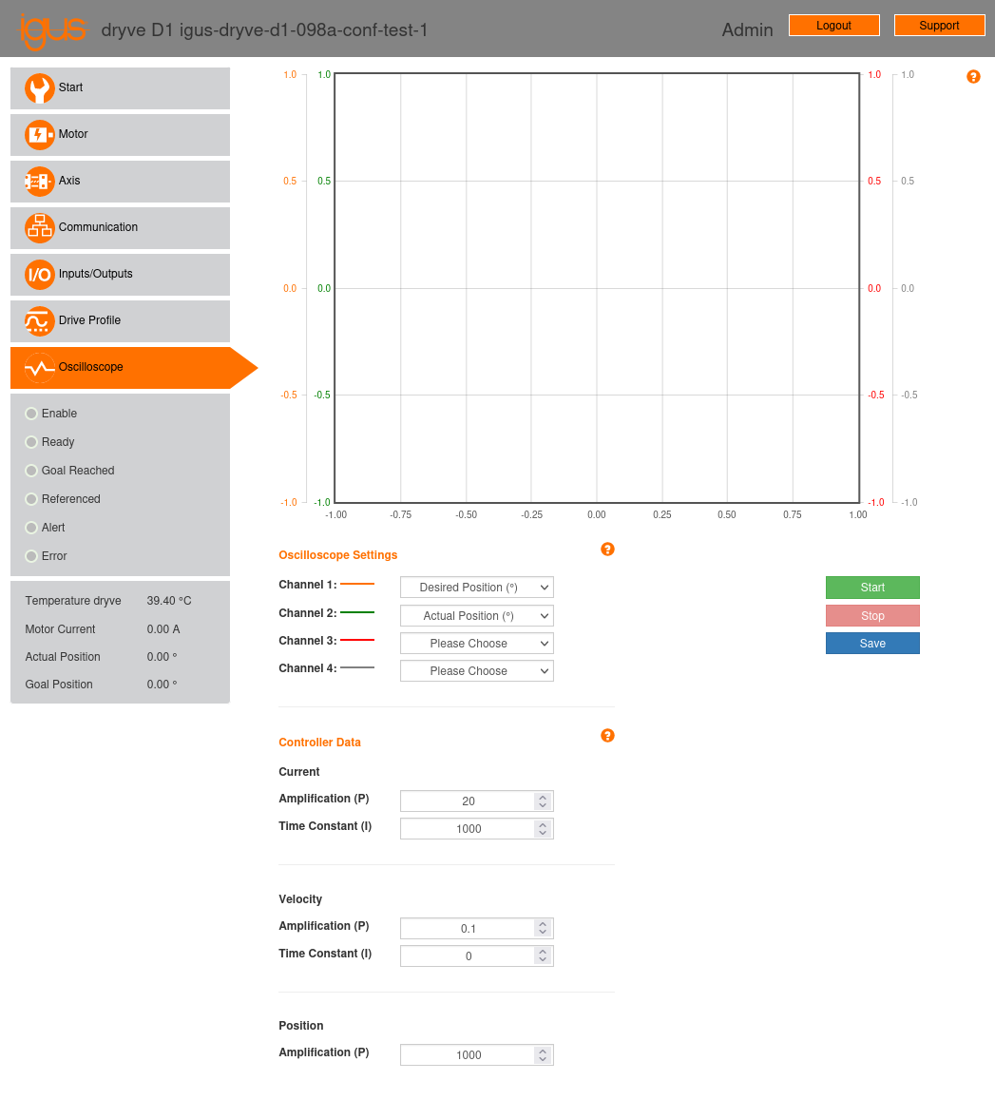
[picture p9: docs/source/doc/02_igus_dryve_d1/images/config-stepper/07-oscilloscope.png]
:::{figure} images/config-stepper/07-oscilloscope.png
:name: fig:conf_brushless_7

"Oscilloscope" configuration page of the stepper motor controller.
:::

## Oscilloscope

The oscilloscope allows for the simultaneous observation of four channels over a 5-second window, enabling a detailed evaluation of motor behavior in real time. Each channel can monitor one of the following values:

- Actual current (A)
- Tracking error
- Speed (rpm)
- Actual position
- Desired position
- Digital inputs
- Analog input 1 (AI 1)
- Analog input 2 (AI 2)

(sec:oscilloscope_parameters)=
## Control Parameters 

:::{figure} images/motor_control/fig.*
:name: fig:motor_control

Closed-loop control of position, speed, and current.
:::

The igus® dryve D1 controller manual does not explicitly describe the control system it implements. We assume that it employs a closed-loop control system with "minor loop feedback compensation" {cite}`enwiki:1032838404,nise2015control,golnaraghi2017automatic`. In this system, the motor's position, speed, and current are used as feedback signals to precisely and dynamically adjust its position. This control system architecture is commonly used in motor control applications. Its structure, considering the {{P}} and {{I}} parameters defined by the igus® dryve D1 controller, is shown in {numref}`fig:motor_control`, where:

- $R(t)$ is the requested position for the motor at time $t$.

- $c(t)$ is the current supplied to the motor at time $t$, used as a feedback parameter for the current controller.

- $p(t)$ is the motor's position at time $t$, obtained from the motor's encoder and used as a feedback parameter for the position controller.

- $v(t)$ is the motor's speed at time $t$, obtained as the derivative with respect to $t$ of the position $p(t)$ and used as a feedback parameter for the speed controller.

- $e_c(t)$ is the current error, calculated as the output of the speed controller minus the current feedback parameter $c(t)$.

- $e_p(t)$ is the position error, calculated as $R(t) - p(t)$.

- $e_v(t)$ is the speed error, calculated as the output of the position controller minus the speed feedback parameter $v(t)$.

- $\kappa_p$ is the proportional parameter for the position controller.

- $\lambda_p$ and $\lambda_i$ are, respectively, the proportional and integral parameters for the speed controller.

- $\mu_p$ and $\mu_i$ are, respectively, the proportional and integral parameters for the current controller.

- $P(\alpha)(t)$ is the impulse response of the proportional block. For an input $x(t)$, the output of the proportional block at time $t$ is:

    $$x(t) * P(\alpha)(t) = \alpha \cdot x(t)$$

- $I(\beta)(t)$ is the impulse response of the integral block. For an input $x(t)$, the output of the integral block at time $t$ is:

    $$x(t) * I(\beta)(t) = \beta \int_{-\infty}^t x(\tau) d\tau$$

The "Oscilloscope" page provides access to the configuration of the {{PI}} controllers parameters. These parameters allow for optimizing motor performance to meet the specific requirements of each task. For igus® motors, by selecting the corresponding motor model in the motor configuration section (see {numref}`sec:motor_motor`), the control parameters will be set to the default values for the chosen motor. In applications involving high speeds, heavy loads, or when noise reduction is critical, fine adjustments to the control parameter configuration may be necessary.

In our testbed setup, we have configured the following parameters for both motors, which have worked well:

- **Current**
  - **Amplification (P)**: 20
  - **Time constant (I)**: 1000
- **Velocity**
  - **Amplification (P)**: 0.1
  - **Time constant (I)**: 0
- **Position**
  - **Amplification (P)**: 1000

:::{note}
When configuring the motor control parameters in the "Oscilloscope" page, it is important to consider the following points:

- Parameters become effective upon pressing "enter" or unfocusing the corresponding parameter input field.
- Parameters require very fine adjustment; an abrupt change in a parameter can cause the corresponding {{PI}} controller to become unstable and result in sudden motor movement. In such a case, if the movement limit parameters have been adequately configured (see {numref}`sec:axis_motion_limits`), the controller should stop the motor and report a tracking error.
- Setting some parameters to excessively high values could lead to unwanted vibrations and noise in the motors due to oscillations in the {{PI}} controller signal. Conversely, setting some parameters to excessively low values could cause the motors to respond slowly to commands issued by the controller.
:::

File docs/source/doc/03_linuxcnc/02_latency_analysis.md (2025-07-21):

# System Latency Analysis

As mentioned in {numref}`sec:linuxcnc_installation`, LinuxCNC requires a real-time operating system (RTOS), a type of operating system designed for real-time device and process control. Unlike traditional operating systems, RTOSs are engineered to ensure that critical tasks are completed within strict time limits. These systems are needed in applications where response time is vital, such as industrial control systems, aircraft navigation systems, and automotive anti-lock braking systems, among others.

There are two primary types of real-time operating systems:

- **Soft Real-Time Systems**: In these systems, critical tasks generally meet their deadlines, but occasional missed deadlines do not lead to severe consequences. These systems prioritize speed and efficiency, allowing some flexibility in timing.
- **Hard Real-Time Systems**: These systems enforce absolute and strict time limits. Critical tasks must be completed within a precise timeframe; otherwise, catastrophic consequences could occur. Hard real-time systems are common in safety-critical applications.

As noted in {numref}`sec:linuxcnc_installation`, our system uses a Linux operating system with `PREEMPT_RT` patches to add real-time capabilities. This is a soft real-time system, meaning that occasional deviations from the scheduled execution intervals of processes may occur. In this context, the critical factor to analyze is latency, or jitter, which refers to temporal variations in task execution intervals.

Historically, one of the most common methods for controlling stepper motors in LinuxCNC has been the software generation of step pulses. In such cases, very low latency, ideally less than 20 μs, is essential to generate pulses frequently enough for precise and consistent motor movement at the required speeds.

In our setup, where MESA boards are used to generate motor control signals, a communication interval of 1 ms is typically sufficient, making latency less critical than in the previous scenario. Here, a maximum latency of 200 μs can be acceptable.

Before running LinuxCNC to control machinery, we should analyze the maximum system latency and confirm that it is adequate. For this purpose, LinuxCNC includes the following tools:

- **Latency Histogram**: `latency-histogram`
- **Latency Plot**: `latency-plot`
- **Latency Test**: `latency-test`

:::{important}
LinuxCNC must not be running when these tools are in use.
:::

:::{important}
To determine the maximum latency, the latency histogram or latency test are the most suitable tools. It is advisable to perform the test for at least several minutes. During the test, the computer should be subjected to a significant load. For example, the LinuxCNC user manual recommends moving windows across the screen, browsing the web, copying large files to disk, playing music, and running intensive programs like `glxgears` in OpenGL.
:::

These tools consider two threads:

- A fast thread, known as the "base thread," with a default period of 25 μs.
- A slower thread, known as the "servo thread," with a default period of 1 ms.

The following sections describe each of these tools.

## Latency Histogram

The `latency-histogram` tool displays a latency histogram for the "base thread" and "servo thread." The available command options are shown in the tool's help text in {numref}`lst:latency-histogram`. The tool's graphical interface is shown in {numref}`fig:linuxcnc_latency_histogram`.

:::{code-block} text
:name: lst:latency-histogram
:caption: Help text for the latency-histogram tool.

Usage:
   latency-histogram --help | -?
or
   latency-histogram [Options]

Options:
  --base      nS   (base  thread interval, default:   25000, min:  5000)
  --servo     nS   (servo thread interval, default: 1000000, min: 25000)
  --bbinsize  nS   (base  bin size,  default: 100)
  --sbinsize  nS   (servo bin size, default: 100)
  --bbins     n    (base  bins, default: 200)
  --sbins     n    (servo bins, default: 200)
  --logscale  0|1  (y axis log scale, default: 1)
  --text      note (additional note, default: "")
  --show           (show count of undisplayed bins)
  --nobase         (servo thread only)
  --verbose        (progress and debug)
  --nox            (no gui, display elapsed,min,max,sdev for each thread)

Notes:
  Linuxcnc and Hal should not be running, stop with halrun -U.
  Large number of bins and/or small binsizes will slow updates.
  For single thread, specify --nobase (and options for servo thread).
  Measured latencies outside of the +/- bin range are reported
  with special end bars.  Use --show to show count for
  the off-chart [pos|neg] bin
:::

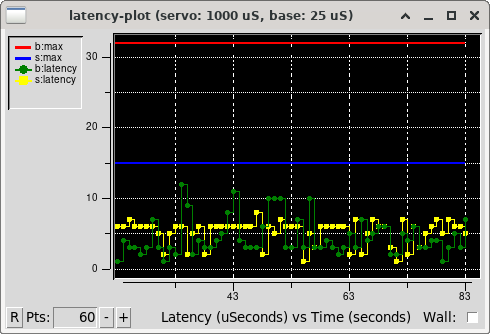
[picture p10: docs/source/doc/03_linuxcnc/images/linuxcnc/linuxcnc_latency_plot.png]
:::{figure} images/linuxcnc/linuxcnc_latency_plot.png
:name: fig:linuxcnc_latency_plot

LinuxCNC latency plot tool.
:::

## Latency Plot

The `latency-plot` tool displays a latency plot for the "base thread" and "servo thread." The available command options are shown in the tool's help text in {numref}`lst:latency-plot`. The tool's graphical interface is shown in {numref}`fig:linuxcnc_latency_plot`.

:::{code-block}
:name: lst:latency-plot
:caption: Help text for the latency-plot tool.

Usage:
      latency-plot --help | -?      (this)
      latency-plot --hal [Options]

Options:
      --base nS  (base  thread interval, default:   25000)
      --servo nS (servo thread interval, default: 1000000)
      --time mS  (report interval, default: 1000)
      --relative (relative clock time (default))
      --actual   (actual clock time)
:::

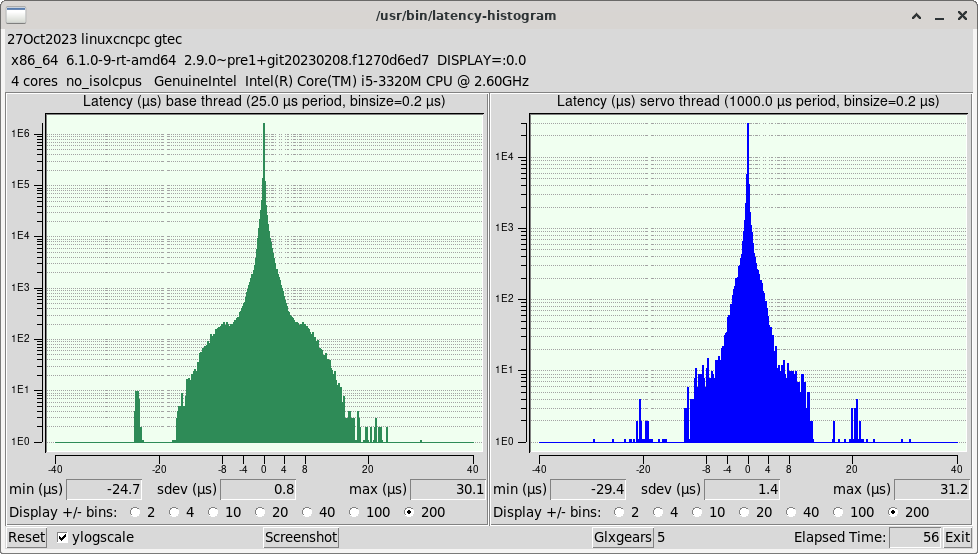
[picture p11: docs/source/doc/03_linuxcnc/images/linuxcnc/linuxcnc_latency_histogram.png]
:::{figure} images/linuxcnc/linuxcnc_latency_histogram.png
:name: fig:linuxcnc_latency_histogram

LinuxCNC latency histogram tool.
:::

## Latency Test

The `latency-test` tool runs a latency test for the "base thread" and "servo thread," reporting the interval and maximum latency for each. The available command options are shown in the tool's help text in {numref}`lst:latency-test`. The tool's graphical interface is shown in {numref}`fig:linuxcnc_latency_test`.

:::{code-block}
:name: lst:latency-test
:caption: Help text for the latency-test tool.

Usage:
       latency-test [base-period [servo-period]]
   or:
       latency-test period -      # for single thread
   or:
       latency-test -h | --help   # (this text)

Defaults:     base-period=25000nS servo-period=1000000nS
Equivalently: base-period=25µs servo-period=1ms

Times may be specified with suffix "s", "ms", "us" "µs", or "ns"
Times without a suffix and less than 1000 are taken to be in us;
other times without a suffix are taken to be in ns

The worst-case latency seen in any run of latency-test
is written to the file ~/.latency
:::

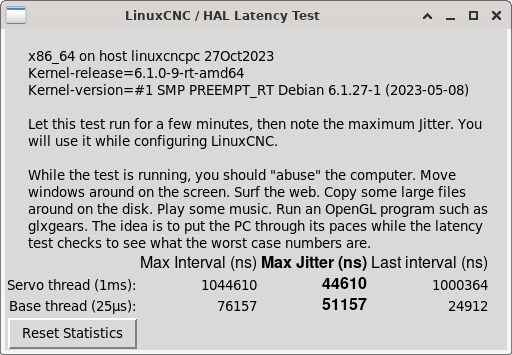
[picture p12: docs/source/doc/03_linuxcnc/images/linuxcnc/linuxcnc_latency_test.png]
:::{figure} images/linuxcnc/linuxcnc_latency_test.png
:name: fig:linuxcnc_latency_test

LinuxCNC latency test tool.
:::

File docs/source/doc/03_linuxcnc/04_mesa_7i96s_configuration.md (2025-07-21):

# MESA 7I96S Board Configuration

## Flashing the Firmware

:::{note}
This process has already been completed and does not need to be repeated; it is described here solely for documentation purposes. For more information on configuring the MESA 7I96S board, please consult its manual.
:::

The MESA 7I96S board can be used standalone with its standard configuration. However, to use it with the MESA 7I77 board, we must flash the FPGA with the appropriate firmware. Various firmwares for the 7I96S board are available on the MESA website at <http://www.mesanet.com/software/parallel/7i96s.zip>.

To use the MESA 7I96S board with the MESA 7I77 board, we will use the `7i96s_7i77d.bin` firmware. First, power the board with 5 V via its P4 connector and connect it to the PC using an Ethernet cable. By default, the board's IP address is `192.168.1.121`. To verify connectivity, execute the following command:

```sh
mesaflash -device 7i96s -addr 192.168.1.121
```

If successful, the `mesaflash` utility will detect the board and respond with the following output:

```text
ETH device 7I96S at ip=192.168.1.121
```

Finally, to flash the firmware to the board, execute the following command:

```sh
mesaflash -device 7i96s -addr 192.168.1.121 -write 7i96s_7i77d.bin
```

## IP Address

The MESA 7I96S board has three options for setting the IP address: a default IP (`192.168.1.121`), an IP read from the EEPROM, and IP acquisition via the BOOTP network protocol. These options are selected using jumpers `W4` and `W5`, located on the bottom left of the board as shown in {numref}`fig:mesa_ip_selection`.

:::{figure} images/mesa/mesa_7i96s_bottom_left_labelled.*
:name: fig:mesa_ip_selection

View of the bottom left side of the MESA 7I96S board.
:::

The available IP configuration options are detailed in {numref}`tab:mesa_ip_selection`. Specifically, note the following:

- When jumpers `W4` and `W5` are in the (down, up) position, the IP address will be read from the EEPROM. The default IP address in the EEPROM is 10.10.10.10. This IP address can be changed using the `mesaflash` utility. For example, to set the IP in the EEPROM to 10.10.10.100, you would execute the following command:

    ```sh
    mesaflash -device 7i96s -addr 192.168.1.121 -set ip=10.10.10.100
    ```

- When jumpers `W4` and `W5` are in the (up, up) position, the IP address will be set to 192.168.1.121, and the board will boot using the fallback configuration (see {numref}`sec:mesa7i96s_fallback`).

:::{csv-table} IP address configuration options on the MESA 7I96S board using jumpers ``W4`` and ``W5``.
:name: tab:mesa_ip_selection
:widths: auto
:header: W4, W5, IP Address

Down, Down, 192.168.1.121
Down, Up, Read from EEPROM
Up, Down, Obtained via BOOTP
Up, Up, 192.168.1.121 and use fallback conf.
:::

In our testbed setup, jumpers `W4` and `W5` have been set to the (down, up) position, as shown in {numref}`fig:mesa_ip_selection`. This configuration allows the board to read the IP address stored in the EEPROM. For this setup, we have configured the board's IP address to 10.68.33.122.

(sec:mesa7i96s_fallback)=
## Fallback Configuration

The MESA 7I96S board's flash memory contains two images: a main image and a fallback image. If the primary image becomes corrupted, the FPGA will load the fallback configuration, allowing a new main image to be written. Otherwise, the memory would have to be programmed via JTAG.

It is possible to force the board to boot using the fallback configuration by setting the IP selection jumpers `W4` and `W5` to the (up, up) position. In this boot mode, the card's IP address will be set to 192.168.1.121.

(sec:mesa7i96s_cable_power)=
## Expansion Connector 5 V Power Supply

The MESA 7I96S board has the capability to supply 5V power to the board connected to its expansion connector (P1), which in our case is the MESA 7I77. This option is controlled by jumper `W6`, located on the bottom of the board to the left of the expansion connector, as shown in {numref}`fig:mesa_ip_selection`. The settings are as follows:

- When jumper `W6` is in the up position, the MESA 7I96S board will provide power to the MESA 7I77 board through the expansion connector.
- When jumper `W6` is in the down position, the MESA 7I96S board will not provide power through the expansion connector; in this case, external power must be supplied to the MESA 7I77 board.

In our testbed setup, the latter option was chosen, with jumper `W6` configured in the down position, as seen in {numref}`fig:mesa_ip_selection`. The MESA 7I77 board must also be configured appropriately, as explained in {numref}`sec:mesa7i77_power`.

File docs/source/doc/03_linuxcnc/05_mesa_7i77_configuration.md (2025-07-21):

# MESA 7I77 Board Configuration

(sec:mesa7i77_power)=
## 5 V Main Power

The MESA 7I77 board can draw its main 5V power either from the MESA 7I96S board or through its `TB1` connector. This power is needed for the encoders, analog outputs, and the RS-422 interface. The main power mode for the MESA 7I77 is selected using jumper `W5` as follows:

1. If `W5` is in the left position, power is supplied via the MESA 7I96S board. In this case, jumper `W6` on the MESA 7I96S board must be set to the up position.
2. If `W5` is in the right position, power must be supplied to the board externally through the `TB1` connector. In this case, jumper `W6` on the MESA 7I96S board must be set to the down position to prevent it from supplying power to the daughterboard.

:::{attention}
Supplying power to the MESA 7I77 board through the `TB1` connector with jumper `W5` in the left position can potentially damage the MESA 7I77 board, the MESA 7I96S board, the connection cable, and even the PC.
:::

In our testbed setup, we chose to power the MESA 7I77 board via the `TB1` connector; therefore:

- Jumper `W6` on the MESA 7I96S board has been set to the down position, as shown in {numref}`fig:mesa_ip_selection`.
- Jumper `W5` on the MESA 7I77 board has been set to the right position, as shown in {numref}`fig:mesa7i77_left`.

:::{figure} images/mesa/mesa_7i77_left_labelled.*
:name: fig:mesa7i77_left

View of the left side of the MESA 7I77 board.
:::

## Digital Inputs and Outputs Power

In addition to the 5V main power, the MESA 7I77 board also requires supplementary power for its digital inputs and outputs through the `TB2` connector (see Figures {numref}`%s <fig:installation>` and {numref}`%s <fig:mesa7i77_right>`). The pinout for the `TB2` connector is provided in {numref}`tab:mesa7i77_tb2`.

:::{csv-table} Connections of the ``TB2`` connector of the MESA 7I77 board.
:name: tab:mesa7i77_tb2
:widths: auto
:header: Pin, Signal, Function

  1 (bottom), `VFIELD`, `FIELD POWER`
  2, `VFIELD`, `FIELD POWER`
  3, `VFIELD`, `FIELD POWER`
  4, `VFIELD`, `FIELD POWER`
  5, `VIN`, `FIELD I/O LOGIC POWER`
  6, Not connected, --
  7, Not connected, --
  8 (top), Ground, Reference of `VIN` & `VFIELD`
:::

As indicated in {numref}`tab:mesa7i77_tb2`, the board requires two power inputs in this configuration:

- `VFIELD`: This input supplies power to the outputs and determines the logic levels of the inputs, with a range of 5 V to 28 V.
- `VIN`: This input provides power to the input/output logic, with a range of 8 V to 32 V.

If `VFIELD` is between 8 V and 28 V, the same source can be used to power `VIN`. The board includes jumper W1, which, when placed in the left position, connects `VIN` with `VFIELD`. To use `VFIELD` values outside the `VIN` range (e.g., 5 V), you must place W1 in the right position to disconnect `VIN` and `VFIELD`, allowing for separate power supplies for `VIN` and `VFIELD`.

:::{attention}
The voltage at `VFIELD` must have a maximum rise rate of 10 V/ms to prevent damage to the board. This is a limitation of MOSFET transistors {cite}`toshiba2018impacts, toshiba2018mosfets, nexperia2023power, bai2003analysis`. Therefore, `VFIELD` must be connected directly to the power supply without using switches in the circuit.
:::

As stated in {numref}`sec:page_input_outputs`, the MESA 7I96S board can only use 5 V logic for step and direction signals. Therefore, the logic for both the igus® dryve D1 controllers and the MESA 7I77 board must also be 5 V. Thus, in our testbed setup, jumper `W1` on the MESA 7I77 board has been set to the right position, the `VIN` input to 24 V, and the `VFIELD` input to 5 V, as shown in {numref}`fig:mesa7i77_right`.

::: {figure} images/mesa/mesa_7i77_right_labelled.*
:name: fig:mesa7i77_right

View of the right side of the MESA 7I77 board.
:::

## Encoder Input Modes

The MESA 7I77 board has six encoder inputs, each with individual A, B, and Z inputs. These inputs can be configured to operate with either differential or single-ended signals. Each encoder has three jumpers to configure the mode for its individual A, B, and Z inputs. Setting a jumper to the right position selects differential mode, while setting it to the left position selects single-ended mode. The list of jumpers for the individual inputs of each encoder is provided in {numref}`tab:encoder_jumpers`.

:::{table} Encoder configuration jumpers.
:name: tab:encoder_jumpers
:widths: auto

| Encoder | Jumper A  | Jumper B | Jumper C |
| --- | --- | --- | --- |
| 0 | W21 | W19 | W17 |
| 1 | W15 | W13 | W10 |
| 2 | W8 | W6 | W2 |
| 3 | W22 | W20 | W18 |
| 4 | W16 | W14 | W11 |
| 5 | W9 | W7 | W3 |
:::

In our testbed setup, the following MESA 7I77 board encoder inputs and modes were used:

- The stepper motor encoder was connected to input 0. This encoder uses differential signals, so jumpers `W21`, `W19`, and `W17` were left in their default right position.
- The brushless motor encoder was connected to input 1. This encoder uses single-ended signals, so jumpers `W15`, `W13`, and `W10` were set to the left position.

The configuration of the aforementioned jumpers for encoders 0 and 1 on the MESA 7I77 board in the testbed setup is shown in {numref}`fig:mesa7i77_left`.

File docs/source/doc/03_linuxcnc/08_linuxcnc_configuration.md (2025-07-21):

(sec:linuxcnc_configuration)=
# LinuxCNC Configuration

As noted in {numref}`sec:linuxcnc_intro_config`, a LinuxCNC configuration comprises several files, requiring at least one INI file and one {{HAL}} file. The following sections detail the configuration of both file types, using the `mesa_7i96s_7i77_xy` configuration as an example.

(sec:linuxcnc_configuration_ini)=
## INI Configuration

### .ini Configuration File Format

An `.ini` file is a plain text file used for configuring applications and programs. It has a simple structure consisting of sections and key-value pairs. The basic syntax of an `.ini` file is as follows:

- **Sections**: Sections serve to organize keys and values. Each section begins with its name enclosed in square brackets, followed by zero or more key-value pairs belonging to that section. The syntax for a section is:

    ```ini
    [section_name]
    ```

- **Keys and Values**: Within each section, keys and their corresponding values can be defined. Keys are identifiers used to access associated values. The syntax for a key-value pair is:

    ```ini
    key = value
    ```

    Keys can contain letters and underscores (`_`). Values can be text strings, integers, or floating-point numbers.

- **Comments**: Comments begin with a semicolon (`;`) or a hash symbol (`#`). For example:

    ```ini
    ; This is a comment
    # This is also a comment
    ```

### Example: `mesa_7i96s_7i77_xy.ini` Configuration File

Below are the different sections of the `mesa_7i96s_7i77_xy.ini` configuration file, with comments explaining the purpose of each parameter. Note that not all available parameters are specified in some sections. For a complete list of parameters and their documentation, consult the LinuxCNC user manual {cite}`linuxcncdoc`.

- **EMC Section**: General configuration.

    :::{literalinclude} codes/mesa_7i96s_7i77_xy.ini
    :language: ini
    :lines: 1-12
    :lineno-match:
    :::

- **DISPLAY Section**: User interface configuration. The available options may depend on the specific user interface used. In this case, we are using the AXIS user interface.

    :::{literalinclude} codes/mesa_7i96s_7i77_xy.ini
    :language: ini
    :lines: 14-64
    :lineno-match:
    :::

- **TASK Section**: LinuxCNC task controller configuration. The task controller is responsible for communicating with the user interface, the motion planner, and the G-code interpreter. Currently, `milltask` is the only task controller available. For more information, consult the LinuxCNC user manual {cite}`linuxcncdoc` and the `milltask` man page, also available at <http://linuxcnc.org/docs/devel/html/man/man1/milltask.1.html>.

    :::{literalinclude} codes/mesa_7i96s_7i77_xy.ini
    :language: ini
    :lines: 67-74
    :lineno-match:
    :::

- **RS274NGC Section**: RS274NGC (G-code) interpreter configuration.

    :::{literalinclude} codes/mesa_7i96s_7i77_xy.ini
    :language: ini
    :lines: 77-84
    :lineno-match:
    :::

- **EMCMOT Section**: Motion controller configuration. The `EMCMOT` and `SERVO_PERIOD` parameters are not directly used by LinuxCNC but are used to configure the motion control module in the {{HAL}} file (see {numref}`sec:linuxcnc_configuration_hal`).

    :::{literalinclude} codes/mesa_7i96s_7i77_xy.ini
    :language: ini
    :lines: 87-100
    :lineno-match:
    :::

- **{{HAL}} Section**: {{HAL}} configuration.

    :::{literalinclude} codes/mesa_7i96s_7i77_xy.ini
    :language: ini
    :lines: 103-117
    :lineno-match:
    :::

- **HALUI Section**: HALUI (HAL-based user interface) configuration. The only available option is `MDI_COMMAND`, which allows MDI commands to be executed via {{HAL}} signals. In our case, this section is left empty.

    :::{literalinclude} codes/mesa_7i96s_7i77_xy.ini
    :language: ini
    :lines: 120-126
    :lineno-match:
    :::

- **KINS Section**: Kinematics configuration.

    :::{literalinclude} codes/mesa_7i96s_7i77_xy.ini
    :language: ini
    :lines: 129-137
    :lineno-match:
    :::

- **APPLICATIONS Section**: LinuxCNC allows applications to be launched at startup. These applications must be specified within the `APPLICATIONS` section using the `APP` option, which can be used multiple times. Applications will be launched either at the beginning, before the graphical interface starts, or after a delay specified by the `DELAY` option.

    :::{literalinclude} codes/mesa_7i96s_7i77_xy.ini
    :language: ini
    :lines: 140-144
    :lineno-match:
    :::

- **TRAJ Section**: Trajectory planner configuration.

    :::{literalinclude} codes/mesa_7i96s_7i77_xy.ini
    :language: ini
    :lines: 147-164
    :lineno-match:
    :::

- **EMCIO Section**: Input/output controller configuration. This controls input/output tasks such as coolant, tool changes, and emergency stops.

    :::{literalinclude} codes/mesa_7i96s_7i77_xy.ini
    :language: ini
    :lines: 167-174
    :lineno-match:
    :::

- **AXIS\_\<i\> Section**: Configuration for axis *\<i\>*. Possible values for *\<i\>* include `X`, `Y`, `Z`, `A`, `B`, `C`, `U`, `V`, and `W`. An example of the X-axis configuration is provided below; the Y-axis configuration is similar.

    :::{important}
    When configuring the robot's limits (`MIN_LIMIT` and `MAX_LIMIT` parameters), it is advisable to leave some margin beyond the desired workspace. If the robot is commanded to position itself at one of the limits, it can easily exceed that limit slightly. For example, if you want your robot to operate on the X-axis between X = 0 and X = 200, you could configure `MIN_LIMIT = -5` and `MAX_LIMIT = 205`.
    :::

    :::{literalinclude} codes/mesa_7i96s_7i77_xy.ini
    :language: ini
    :lines: 177-190
    :lineno-match:
    :::

- **JOINT\_\<n\> Section**: Configuration for joint (motor) *\<n\>*, where *\<n\>* is the joint number, ranging from 0 to (*\<num_joints\>* $-$ 1). The value of *\<num_joints\>* is set in the `JOINTS` option of the `KINS` section.

    For machines with Cartesian geometries, such as gantry robots, LinuxCNC includes the `trivkins` kinematics module. With this module, by default, there is a 1:1 correspondence between the axis coordinate letter and the joint number, i.e., JOINT_0 = X, JOINT_1 = Y, ..., JOINT_8 = W.

    The `trivkins` module accepts the `coordinates` parameter to specify the association of axis coordinate letters with the joint number. For example, with the parameter `coordinates=XZ`, JOINT_0 will be assigned to X and JOINT_1 to Z. In this parameter, the same axis letter can be specified multiple times, allowing multiple joints to be assigned to the same axis. In this case, it is also necessary to use the `kinstype=B` parameter. For instance, with the parameters `coordinates=XX` and `kinstype=B`, both JOINT_0 and JOINT_1 will be assigned to X.

    For more information about the `trivkins` kinematics module, consult the `kins` man page, also available at <http://linuxcnc.org/docs/devel/html/man/man9/kins.9.html>.

    :::{important}
    Both the joint and axis configurations include `MAX_VELOCITY`, `MAX_ACCELERATION`, `MIN_LIMIT`, and `MAX_LIMIT` parameters. When the robot is not homed, LinuxCNC uses the parameters from the joint sections; however, once the robot is homed, it uses the parameters from the axis sections.
    :::

    The following code shows the configuration of joint 1 (X-axis), which corresponds to the stepper motor. The parameters specified below the comment "Custom configurations for the HAL file" are not directly used by LinuxCNC; they are used to configure the motor parameters in the {{HAL}} file (see {numref}`sec:linuxcnc_configuration_hal`).

    :::{literalinclude} codes/mesa_7i96s_7i77_xy.ini
    :language: ini
    :lines: 193-299
    :lineno-match:
    :::

    The following code shows the configuration of joint 2 (Y-axis), which corresponds to the brushless motor. As before, the parameters specified below the comment "Custom configurations for the HAL file" are not directly used by LinuxCNC; they are used to configure the motor parameters in the {{HAL}} file (see {numref}`sec:linuxcnc_configuration_hal`). These parameters differ from the previous ones because now a brushless motor is used.

    :::{literalinclude} codes/mesa_7i96s_7i77_xy.ini
    :language: ini
    :lines: 318-409
    :lineno-match:
    :::

(sec:linuxcnc_configuration_hal)=
## {{HAL}} Configuration

{{HAL}} is a fundamental component of LinuxCNC, serving as an interface between the machine's software and hardware. It provides the infrastructure for communication among the system's numerous software and hardware components. The {{HAL}} layer is composed of components that:

- Are interconnected, processing incoming data and providing outputs to other components (e.g., the motion planning algorithm instructs the motors on their movement).
- Possess the ability to communicate with hardware.
- Always run periodically in one of the following ways:
  - As real-time components, either with an execution frequency of a few microseconds (e.g., to advance a stepper motor or read an encoder) or with a frequency less than one millisecond (e.g., to adjust the planning of subsequent movements to complete a G-code instruction).
  - As non-real-time user-space components, which can be interrupted or delayed if the rest of the system is busy or overloaded.

The {{HAL}} components included with LinuxCNC are listed in the user manual {cite}`linuxcncdoc`, also available at <http://linuxcnc.org/docs/stable/html/hal/components.html>. Additionally, each component has its own man page.

### Basic Concepts

- **Pins and Signals**: {{HAL}} is based on the same principles used to design electrical circuits and hardware systems, employing "pins" and "signals" to represent the flow of data between {{HAL}} modules or components. In summary:

  - Pins can carry boolean, float, and signed or unsigned integer values.
  - Pins have a direction: input (IN), output (OUT), or input/output (I/O).
  - A signal identifies a connection between pins.

    {numref}`fig:hal_circuit_concept` from the LinuxCNC documentation {cite}`linuxcncdoc` illustrates the concepts of components, pins, and signals in {{HAL}}. In the figure, pin `pin3-out` of `component.0` connects to pins `pin3-in` and `pin4-in` of `component.1` (via the `signal-red` signal), and pin `pin1-out` of `component.1` connects to pin `pin1-in` of `component.0` (via the `signal blue` signal).

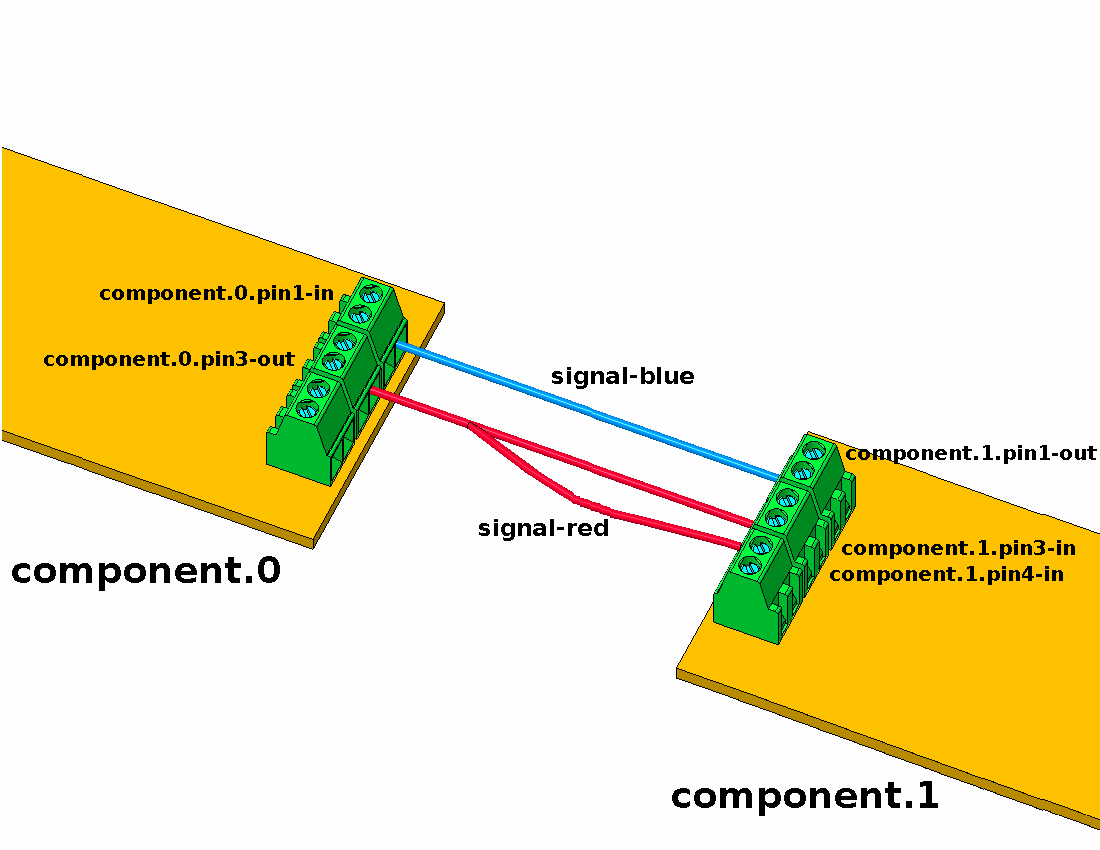
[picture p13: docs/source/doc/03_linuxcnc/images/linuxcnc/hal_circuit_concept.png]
    :::{figure} images/linuxcnc/hal_circuit_concept.png
    :name: fig:hal_circuit_concept

    {{HAL}} Concept --- Connection as electrical circuits. Source: LinuxCNC documentation {cite}`linuxcncdoc`.
    :::

- **Parameters**: {{HAL}} components can have parameters, which are input or output settings not connected to any other component. There are two types of parameters:

  - **Input parameters**: Values that the user can adjust and that remain fixed once configured.
  - **Output parameters**: Values that cannot be adjusted by the user. They allow for internal signals to be monitored.

- **Functions**: Each {{HAL}} component has one or more functions that must be executed to perform the component's task. For these functions to be executed, they must be added to a thread.

- **Threads**: Threads enable {{HAL}} component functions to be executed at specific time intervals. When a thread is created, the time interval at which its assigned functions will be executed is specified. Subsequently, the functions of the {{HAL}} components can be added to the thread to be executed in order at the thread's defined time interval.

### Interaction with {{HAL}} and Commands

{{HAL}} does not interact directly with the user. LinuxCNC provides various interfaces to configure or interact with {{HAL}}:

- From `.hal` files.
- From the command line using the `halcmd` command.
- From Python scripts.
- From C/C++ programs.

Configuration or interaction with {{HAL}} using any of these interfaces is performed through commands. The complete list of commands is detailed in the `halcmd` man page, also available at <http://linuxcnc.org/docs/html/man/man1/halcmd.1.html>. The most relevant commands are:

:::{note}
Generally, each command must be specified on a single line. If a command needs to be split across multiple lines, a backslash (`\`) character can be used to indicate that the line continues to the next. The backslash must be the last character before the new line.
:::

- `loadrt`: Loads a {{HAL}} real-time component into the system. The basic syntax of the `loadrt` command is:

    ```text
    loadrt <component> <options>
    ```

    where `<component>` is the name of the component and `<options>` are the component options. For example:

    ```hal
    loadrt mux4 count=1
    ```

- `addf`: Adds a function to a real-time thread. The syntax of the `addf` command is:

    ```text
    addf <function> <thread>
    ```

    where `<function>` is the name of the function and `<thread>` is the thread to which it will be added. For example:

    ```hal
    addf mux4.0 servo-thread
    ```

- `loadusr`: Loads a non-real-time {{HAL}} component into the system. Non-real-time components are separate processes that can optionally communicate with other {{HAL}} components via pins and parameters. Real-time components cannot be loaded into non-real-time space. The syntax of the `loadusr` command is:

    ```text
    loadusr [<flags>] <command>
    ```

    where `<command>` is the program command to be executed and `<flags>` can be one or more of the following options:

  - `-i`: Ignore the program's return value (with `-w`).
  - `-w`: Wait for the program to finish.
  - `-W`: Wait for the component to be ready. It is assumed that the component will have the same name as the first argument of the command.
  - `-Wn``<name>`: Wait for the component to be ready and assign it the name `<name>`. This is only applicable if the component has the `-n` option to assign a name.

    For example:

    ```hal
    loadusr -Wn spindle gs2_vfd -n spindle
    ```

- `net`: Creates a connection between a signal and one or more pins. The syntax is as follows:

    ```text
    net <signal> <pin>
    ```

    where `<signal>` is the name of the signal and `<pin>` is the name of a pin. If the signal does not exist, a new signal is created. The command also allows the use of the words `<=`, `=>`, and `<=>`, separated by a space from the pin names, to indicate the direction of the signals between pins. These words are ignored by the command and merely serve to facilitate readability.

    The following rules must be met to connect a pin to a signal:

  - An input (IN) pin can always be connected to a signal.
  - An input/output (I/O) pin can be connected unless there is an output (OUT) pin on the signal.
  - An output (OUT) pin can be connected only if there are no other output (OUT) or input/output (I/O) pins on the signal.

    The same signal name can be used in multiple `net` commands to connect additional pins, provided the above rules are respected.

    Examples:

    - ```hal
       net home-x joint.0.home-sw-in <= parport.0.pin-11-in
       ```

       where `home-x` is the signal name, `joint.0.home-sw-in` is an input (IN) pin, `<=` is the optional direction arrow (ignored by the command), and `parport.0.pin-11-in` is an output (OUT) pin.

       This example can also be equivalently defined in {{HAL}} by two `net` commands:

       ```hal
       net home-x <= parport.0.pin-11-in
       net home-x => joint-0.home-sw-in
       ```

       :::{note}
       As seen in this example, although the second pin's name has the `-in` suffix, {{HAL}} treats it as an output pin. Therefore, when configuring pin connections in {{HAL}}, always refer to how the pin is configured in {{HAL}}, not just its name.
       :::

    - ```hal
      net xStep stepgen.0.out => parport.0.pin-02-out parport.0.pin-08-out
      ```

      where `xStep` is the signal name, `stepgen.0.out` is an output pin, and `parport.0.pin-02-out` and `parport.0.pin-08-out` are input pins.

      This example can also be defined in {{HAL}} by two `net` commands as follows:

      ```hal
      net home-x <= stepgen.0.out
      net home-x => parport.0.pin-02-out parport.0.pin-08-out
      ```

- `setp`: Sets the value of a pin or parameter. Valid values depend on the pin or parameter's data type. The syntax of this command is:

    ```text
    setp <name> <value>
    ```

    where `<name>` is the name of the pin or parameter and `<value>` is the value to which it is to be set. The command will fail if `<name>` does not exist as a pin or parameter, if it is a read-only parameter, if it is an output (OUT) pin, if it is a pin that is already connected to a signal, or if `<value>` is not a valid value for the pin or parameter's data type.

- `sets`: Sets the value of a signal. The syntax is:

    ```text
    sets <signal> <value>
    ```

    where `<signal>` is the name of the signal and `<value>` is the value to which it is to be set. The command will fail if `<signal>` does not exist as a signal, if the signal is already connected to an output (OUT) pin, or if `<value>` is not a valid value for the signal's data type.

- `unlinkp`: Unlinks a pin from its connected signal. The syntax of the command is:

    ```hal
    unlinkp <name>
    ```

    where `<name>` is the name of the pin. If the pin does not have a connected signal, nothing happens. The command will fail if `<name>` does not exist as a pin.

### .hal File Format

A `.hal` file is a plain text file containing {{HAL}} commands. Comments can be included by starting lines with the hash symbol (`#`). Options from the `.ini` file can be accessed with the syntax `[<section>]<option>`, where `[<section>]` is the section name in square brackets and `<option>` is the corresponding option name within that section.

### Example: `mesa_7i96s_7i77_xy.hal` Configuration File

As noted in {numref}`sec:linuxcnc_intro_config`, a LinuxCNC configuration includes at least one `.ini` file and one `.hal` file. Below is the `mesa_7i96s_7i77_xy.hal` configuration file, corresponding to the `mesa_7i96s_7i77_xy.ini` file detailed in {numref}`sec:linuxcnc_configuration_ini`. Unlike the `.ini` format, the `.hal` format does not have a formal section syntax; however, for clarity, the file is presented below divided into different parts.

- **Load modules, add functions to threads, and other initial configurations**:

    :::{literalinclude} codes/mesa_7i96s_7i77_xy.hal
    :language: hal
    :lines: 1-54
    :lineno-match:
    :::

- **X-axis configuration (joint 0, stepper motor)**:

    :::{literalinclude} codes/mesa_7i96s_7i77_xy.hal
    :language: hal
    :lines: 57-120
    :lineno-match:
    :::

- **Y-axis configuration (joint 1, brushless motor)**:

    :::{literalinclude} codes/mesa_7i96s_7i77_xy.ini
    :language: hal
    :lines: 123-179
    :lineno-match:
    :::

- **Other configurations**:

    :::{literalinclude} codes/mesa_7i96s_7i77_xy.hal
    :language: hal
    :lines: 182-265
    :lineno-match:
    :::

## {{HAL}} Tools

Several {{HAL}} tools are available for real-time visualization and diagnosis of pin states. The most notable ones are described below; for a complete list of tools, consult the LinuxCNC user manual {cite}`linuxcncdoc`.

### Halcmd

`halcmd` is a command-line tool for interacting with {{HAL}}. When `halcmd` is executed, the following command line will appear:

```text
halcmd:
```

This prompt allows you to enter and execute {{HAL}} commands. Besides the commands detailed previously in {numref}`sec:linuxcnc_configuration_hal`, other commands such as `show`, `list`, or `save` can be very useful. These commands enable printing various elements defined in {{HAL}}, such as pins, parameters, threads, etc. The complete list of commands is detailed in the `halcmd` man page, also available at <http://linuxcnc.org/docs/html/man/man1/halcmd.1.html>.

### Halshow

`halshow` is a graphical tool that allows viewing and monitoring {{HAL}} components such as pins, parameters, signals, and functions. This tool is shown in Figures {numref}`%s <fig:halshow_show>` and {numref}`%s <fig:halshow_watch>`. The tool has the following main elements:

- A tree view displaying {{HAL}} pins, parameters, signals, functions, etc. This view is located on the left side of the window, as seen in Figures {numref}`%s <fig:halshow_show>` and {numref}`%s <fig:halshow_watch>`.
- A text input field for executing {{HAL}} commands, located at the bottom, as shown in Figures {numref}`%s <fig:halshow_show>` and {numref}`%s <fig:halshow_watch>`.
- A "SHOW" tab where information about the selected element in the tree view is displayed, as shown in {numref}`fig:halshow_show`.
- A "WATCH" tab where you can monitor and set values of {{HAL}} pins or parameters. Elements can be added here by clicking on them in the tree view, as shown in {numref}`fig:halshow_watch`.
- A "SETTINGS" tab with various options such as refresh interval or display format of parameters.

The {menuselection}`File` menu allows saving monitored elements from the "WATCH" tab to a file, as well as loading an existing list of elements to monitor from a file.

You can open the Halshow tool from the AXIS graphical interface by clicking on {menuselection}`Machine --> Show Hal Configuration`.

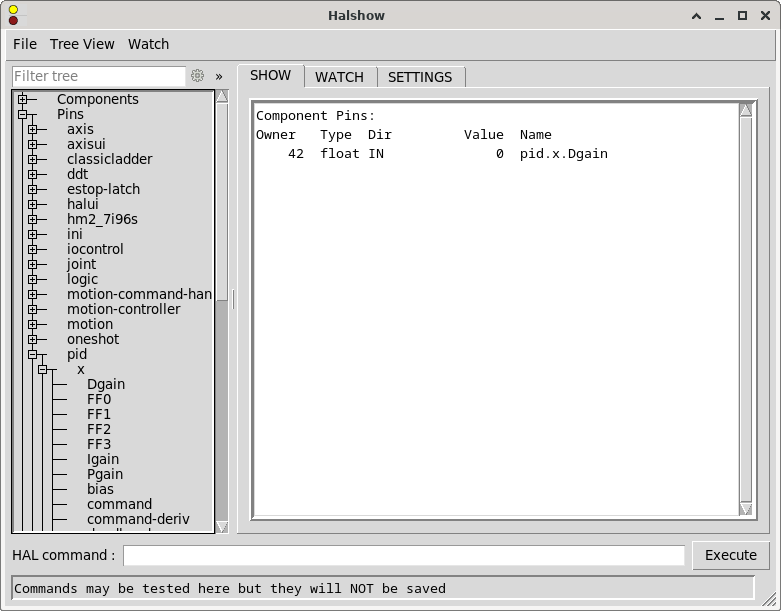
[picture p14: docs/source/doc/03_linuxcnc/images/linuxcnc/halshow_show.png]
:::{figure} images/linuxcnc/halshow_show.png
:name: fig:halshow_show
:width: 70%

Halshow tool showing the "SHOW" tab.
:::

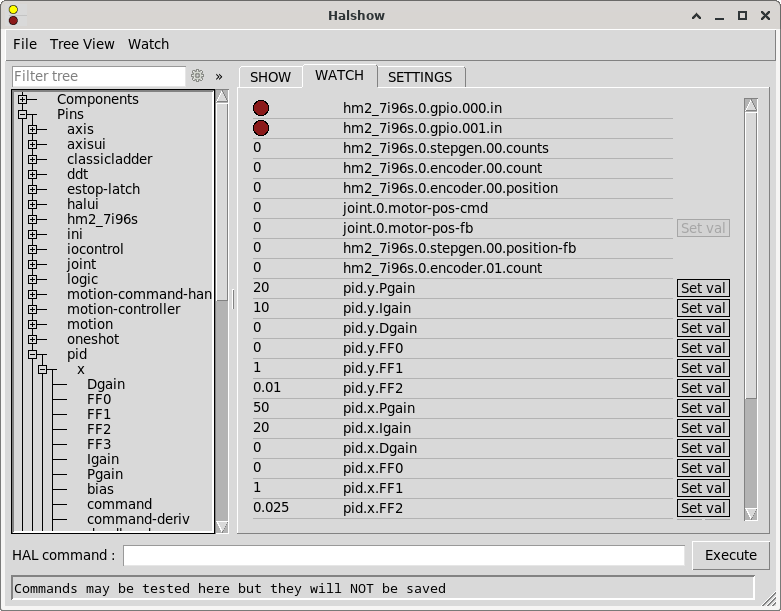
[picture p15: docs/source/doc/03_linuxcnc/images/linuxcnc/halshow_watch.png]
:::{figure} images/linuxcnc/halshow_watch.png
:name: fig:halshow_watch
:width: 70%

Halshow tool showing the "WATCH" tab.
:::

### Halscope

`halscope` is a graphical tool that provides an oscilloscope for {{HAL}}. It allows capturing and displaying the values of pins, signals, and parameters over a period of time. This tool is shown in {numref}`fig:halscope`. The {menuselection}`File` menu allows saving the current configuration or opening a previously saved configuration. When `halscope` is closed, the configuration is automatically saved to the `autosave.halscope` file.

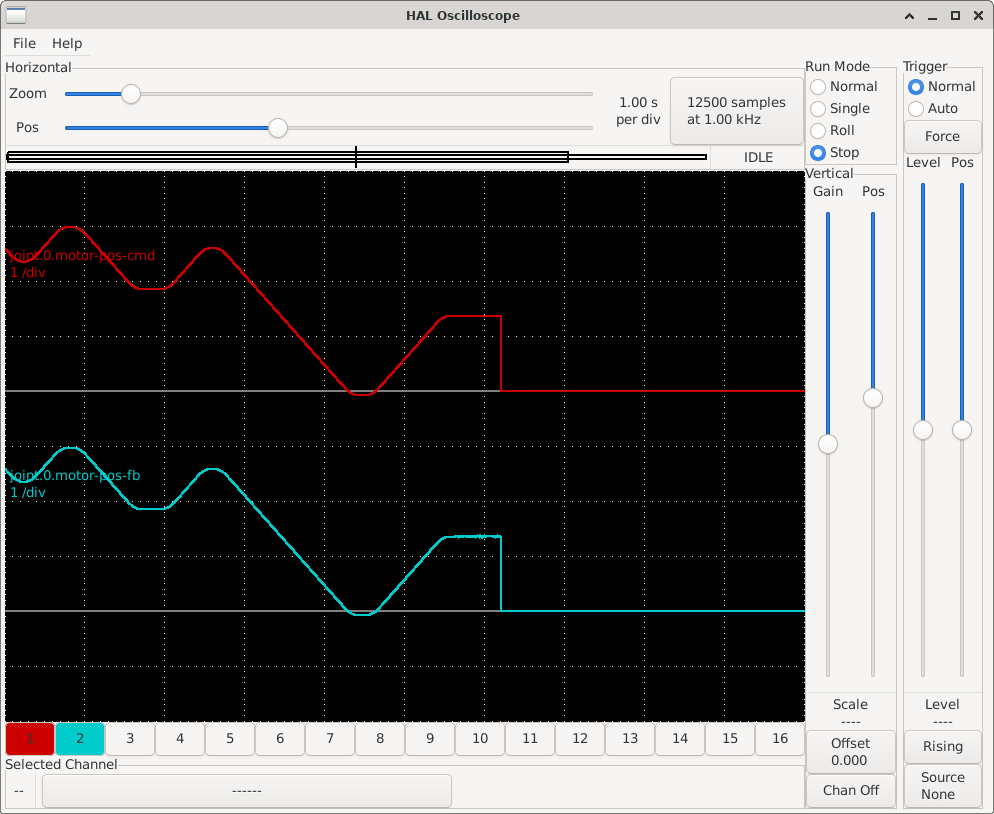
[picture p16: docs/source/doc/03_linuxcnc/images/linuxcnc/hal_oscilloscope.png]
:::{figure} images/linuxcnc/hal_oscilloscope.png
:name: fig:halscope

Halscope tool showing the values of `joint.0.motor-pos-cmd` (motor position commanded by LinuxCNC) and `joint.0.motor-pos-fb` (motor position read from the encoder) over time.
:::

You can open the Halscope tool from the AXIS graphical interface by clicking on {menuselection}`Machine --> Hal scope`.

### Halreport

`halreport` is a command-line tool that generates a report on {{HAL}} connections. The command's help output is as follows:

```text
Usage:
    halreport -h | --help (this help)
or
    halreport [outfilename]
```

The generated report displays all signal connections and indicates potential issues. The information included in the report, among other things, is:

- System description and kernel version.
- Signals and their connected output, input, and input/output pins.
- Functions, threads, and `addf` commands corresponding to each pin.
- Real names for pins that use aliases.
- Signals without an output.
- Signals without inputs.
- Functions not added to threads.
- Warnings about components marked as obsolete.

## Ladder Logic Programming

LinuxCNC includes the ClassicLadder component, a free implementation of a ladder interpreter published under the [{{LGPL}}](https://gnu.org/licenses/lgpl.html).

Ladder logic, or the ladder programming language, is a method for drawing electrical logic diagrams. Originally conceived to describe control systems using relays, this approach has become a widely used graphical language for programming {{PLC}} devices. It derives its name from the fact that programs in this language resemble ladders, with two vertical rails and a series of horizontal rungs between them.

To use ClassicLadder, you must load the `classicladder_rt` real-time module in {{HAL}} and add the `classicladder.0.refresh` function to the `servo-thread` thread using the following commands:

```hal
loadrt classicladder_rt addf classicladder.0.refresh servo-thread
```

Once this is done, you can open the ClassicLadder graphical interface with the system command `classicladder`, or from the AXIS interface by clicking on {menuselection}`File --> Ladder Editor...`. The ClassicLadder graphical interface allows you to create ladder logic programs, as well as view the logical status of the different program components. This interface is composed of several windows, as shown in {numref}`fig:classicladder`.

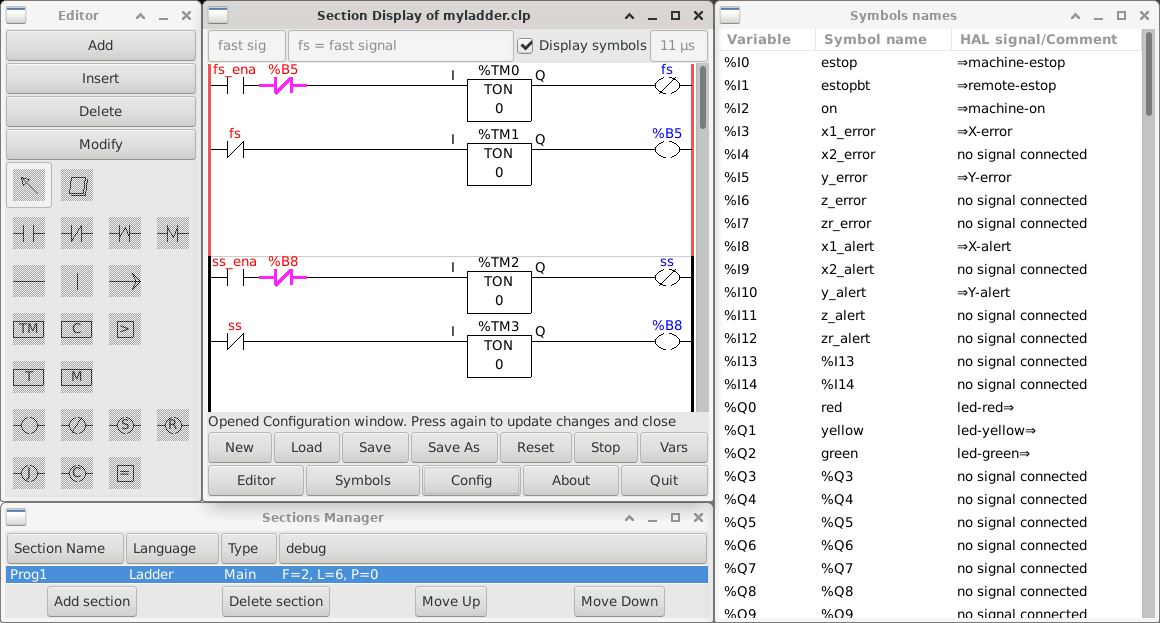
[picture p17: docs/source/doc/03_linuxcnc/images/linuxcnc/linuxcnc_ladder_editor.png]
:::{figure} images/linuxcnc/linuxcnc_ladder_editor.png
:name: fig:classicladder

ClassicLadder graphical interface.
:::

In our testbed setup, ladder logic has been used to program the operation of the LED indicator panel. The program created with ClassicLadder has been saved in the `myladder.clp` file. To use it in LinuxCNC, it can be loaded with the following {{HAL}} command:

```hal
loadusr classicladder myladder.clp -nogui
```

The LinuxCNC user manual {cite}`linuxcncdoc` includes a detailed guide to ClassicLadder. Another good introduction to ClassicLadder is "The Feral Engineer"'s "Classicladder tutorials" series on YouTube: <https://www.youtube.com/playlist?list=PLTYvfbjLClpfAfJSGhZUecgXFwVPY5e09>.

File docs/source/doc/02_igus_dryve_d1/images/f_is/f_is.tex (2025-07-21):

\begin{tikzpicture}
    \def\VMax{10}
    \def\VDeadBand{3}
    
    \begin{axis}[
        % height=6cm,
        % width=10cm,
        xlabel={Input voltage (\unit{\V})},
        ylabel={Output voltage (\unit{\V})},
        xmin=-11,
        xmax=11,
        ymin=-11,
        ymax=11,
        xtick={-\VMax, -\VDeadBand, 0, \VDeadBand, \VMax},
        xticklabels={
            $-V_{\text{max}}$,
            $-V_{\text{ISdb}}$,
            0,
            $V_{\text{ISdb}}$,
            $V_{\text{max}}$
        },
        ytick={-\VMax, -\VDeadBand, 0, \VDeadBand, \VMax},
        yticklabels={
            $-V_{\text{max}}$,
            $-V_{\text{ISdb}}$,
            0,
            $V_{\text{ISdb}}$,
            $V_{\text{max}}$
        },
        grid=both,
    ]
    % Recta 1
    \addplot [domain=-\VMax:-\VDeadBand, thick] {x};

    % Recta 2
    \addplot [thick,dashed] coordinates {(-\VDeadBand,-\VDeadBand) (-\VDeadBand,0)};
    \addplot [domain=-\VDeadBand:\VDeadBand, thick] {0};
    \addplot [thick,dashed] coordinates {(\VDeadBand,0) (\VDeadBand,\VDeadBand)};

    % Recta 3
    \addplot [domain=\VDeadBand:\VMax, thick] {x};
    
    \end{axis}
\end{tikzpicture}

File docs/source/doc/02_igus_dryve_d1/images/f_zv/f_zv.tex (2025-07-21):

\begin{tikzpicture}
    \def\VMax{10}
    \def\VDeadBand{3}
    
    \begin{axis}[
        % height=6cm,
        % width=10cm,
        xlabel={Input voltage (\unit{\V})},
        ylabel={Target position or velocity},
        xmin=-11,
        xmax=11,
        ymin=-1.25,
        ymax=1.25,
        xtick={-\VMax, -\VDeadBand, 0, \VDeadBand, \VMax},
        xticklabels={
            $-V_{\text{max}}$,
            $-V_{\text{ZVdb}}$,
            0,
            $V_{\text{ZVdb}}$,
            $V_{\text{max}}$
        },
        ytick={-1, 0, 1},
        yticklabels={$-o_{\text{max}}$, 0, $o_{\text{max}}$},
        grid=both,
    ]
    % Recta 1
    \addplot [domain=-\VMax:-\VDeadBand, thick] {(x + \VDeadBand)/(\VMax - \VDeadBand)};

    % Recta 2
    \addplot [domain=-\VDeadBand:\VDeadBand, thick] {0};

    % Recta 3
    \addplot [domain=\VDeadBand:\VMax, thick] {(x - \VDeadBand)/(\VMax - \VDeadBand)};
    
    \end{axis}
\end{tikzpicture}

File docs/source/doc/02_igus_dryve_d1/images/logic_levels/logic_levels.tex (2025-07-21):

\begin{tikzpicture}
    % Draw rectangle representing voltage levels
    \draw[fill=gray!20] (0,0) rectangle (3,6);
    
    % Mark voltage levels
    \draw[fill=white] (0,0.6) rectangle (3,3.6);

    \node[right] at (3,6) {Voltage in X2.11};
    \node[right] at (3,3.6) {\qty{60}{\percent} of X2.11};
    \node[right] at (3,0.6) {\qty{10}{\percent} of X2.11};
    \node[right] at (3,0) {\qty{0}{\V}};

    % Add labels for logic states
    \node[] at (1.5, 4.8) {High value};
    \node[] at (1.5, 2.1) {Undefined value};
    \node[] at (1.5, 0.3) {Low value};

    % Draw arrows for voltage levels
    \draw[-{Stealth[length=3mm]}] (-1.5, 0) -- ++(0, 6.5) node[above,midway,rotate=90] {Voltage};
\end{tikzpicture}

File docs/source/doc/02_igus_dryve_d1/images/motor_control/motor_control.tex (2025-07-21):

\begin{tikzpicture}[
    auto,
    piblock/.style = {
        draw,
        rectangle,
        fill=white,
        inner sep=0pt,
        minimum height=0.6cm,
        minimum width=1.1cm
    },
    op/.style = {
        draw,
        circle,
        inner sep=0pt,
        minimum size=15pt
    },
]
    \def\piblocksep{15pt}

    \matrix [
        ampersand replacement=\&,
        column sep=25pt,
        row sep={15pt,between origins}
    ] {
        % First row
        \coordinate (init);
        \& \node [op] (pos_input_sum) {$+$};
        \& \node [piblock] (pos_block_p) {$P(\kappa_p)$};
        \& [-10pt] \node [op] (vel_input_sum) {$+$};
        \& \coordinate (vel_input_1);
        \& [-18pt] \coordinate (vel_input_2);
        \& [-15pt] {
                \node [piblock,yshift=\piblocksep] (vel_block_p) {$P(\lambda_p)$};
                \node [piblock,yshift=-\piblocksep] (vel_block_i) {$I(\lambda_i)$};
            }
        \& [-22pt] \node [op] (vel_inner_sum) {$+$};
        \& [-10pt] \node [op] (cur_input_sum) {$+$};
        \& \coordinate (cur_input_1);
        \& [-18pt] \coordinate (cur_input_2);
        \& [-15pt] {
                \node [piblock,yshift=\piblocksep] (cur_block_p) {$P(\mu_p)$};
                \node [piblock,yshift=-\piblocksep] (cur_block_i) {$I(\mu_i)$};
            }
        \& [-22pt] \node [op] (cur_inner_sum) {$+$};
        \& [-10pt] \node [draw, align=center] (power_mgmt) {Power\\ management};
        \& [-10pt] \node [draw, align=center] (motor) {Motor};
        \\ [35pt]

        % Second row
        \& \&
        \& \node [draw] (d_dt) {$\dfrac{d}{dt}$};
        \& \& \& \& \& \& \& \& \&
        \& \coordinate (power_mgmt_fb1);
        \\ [15pt]

        % Third row
        \& \&
        \& \coordinate (d_dt_pos);
        \& \& \& \& \& \& \& \& \& \&
        \& \coordinate (motor_fb1);
        \\
    };

    \begin{scope}[
        dot/.style = {radius=1.25pt}
    ]
        \draw [->] (init) -- node {$R(t)$} (pos_input_sum);
        \draw [->] (pos_input_sum) -- node {$e_p(t)$} (pos_block_p);
        \draw [->] (pos_block_p) -- (vel_input_sum);
        
        \draw [-]  (vel_input_sum) -- node {$e_v(t)$} (vel_input_1);
        \draw [-]  (vel_input_1) -- (vel_input_2);
        \fill (vel_input_2) circle [dot];
        \draw [->] (vel_input_2) |- (vel_block_p);
        \draw [->] (vel_input_2) |- (vel_block_i);
        \draw [->] (vel_block_p) -| (vel_inner_sum);
        \draw [->] (vel_block_i) -| (vel_inner_sum);

        \draw [->] (vel_inner_sum) -- (cur_input_sum);
        \draw [-]  (cur_input_sum) -- node {$e_c(t)$} (cur_input_1);

        \draw [-]  (cur_input_1) -- (cur_input_2);
        \fill (cur_input_2) circle [dot];
        \draw [->] (cur_input_2) |- (cur_block_p);
        \draw [->] (cur_input_2) |- (cur_block_i);
        \draw [->] (cur_block_p) -| (cur_inner_sum);
        \draw [->] (cur_block_i) -| (cur_inner_sum);
        
        \node [
            draw,
            fit={(vel_input_2) (vel_block_p) (vel_block_i) (vel_inner_sum)}
        ] (vel_block) {};

        \node [
            draw,
            fit={(cur_input_2) (cur_block_p) (cur_block_i) (cur_inner_sum)}
        ] (cur_block) {};

        \node [above=5pt of pos_block_p,align=center,font=\normalsize]
            {Position\\ controller};

        \node [above=5pt of vel_block,align=center,font=\normalsize]
            {Velocity\\ controller};

        \node [above=5pt of cur_block,align=center,font=\normalsize]
            {Current\\ controller};

        \draw [->] (cur_inner_sum) -- (power_mgmt);
        \draw [->] (power_mgmt) -- (motor);

        \draw [->] (power_mgmt) -- (power_mgmt_fb1) -| (cur_input_sum)
            node [below left=5pt,xshift=3pt] {$-$};

        \node [above]
            at ($(cur_input_sum |- power_mgmt_fb1)!0.5!(power_mgmt_fb1)$])
            {$c(t)$};

        \draw [->] (motor) -- (motor_fb1) -| (pos_input_sum)
            node [below left=5pt,xshift=3pt] {$-$};

        \node [above] at ($(d_dt_pos)!0.5!(motor_fb1)$) {$p(t)$};
        
        \fill (d_dt_pos) circle [dot];
        \draw [->] (d_dt_pos) -- (d_dt);
        \draw [->] (d_dt) -- node [right] {$v(t)$} (vel_input_sum)
            node [below left=5pt,xshift=3pt] {$-$};
    \end{scope}
\end{tikzpicture}

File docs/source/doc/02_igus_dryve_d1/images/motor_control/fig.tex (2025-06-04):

\documentclass[tikz]{standalone}
\usepackage{amsmath}
\usepackage[sfdefault]{plex-sans}

\usetikzlibrary{
    calc,
    fit,
    positioning
}

\begin{document}
    \input{motor_control.tex}
\end{document}

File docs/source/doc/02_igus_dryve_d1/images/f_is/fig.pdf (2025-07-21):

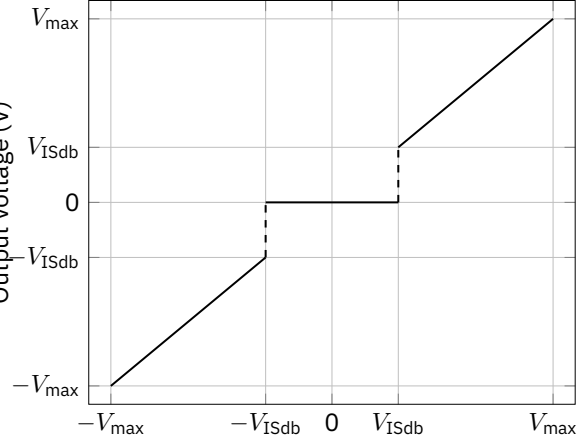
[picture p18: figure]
Vmax; VISdb; VISdb0 VISdb Vmax

## Input voltage (V)

## Output voltage (V)

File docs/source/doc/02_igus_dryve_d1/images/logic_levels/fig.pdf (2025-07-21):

Voltage in X2.11

60 % of X2.11

10 % of X2.11
0 V

High value

Undefined value

Low value

Voltage

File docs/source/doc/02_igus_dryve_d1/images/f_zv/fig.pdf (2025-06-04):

−

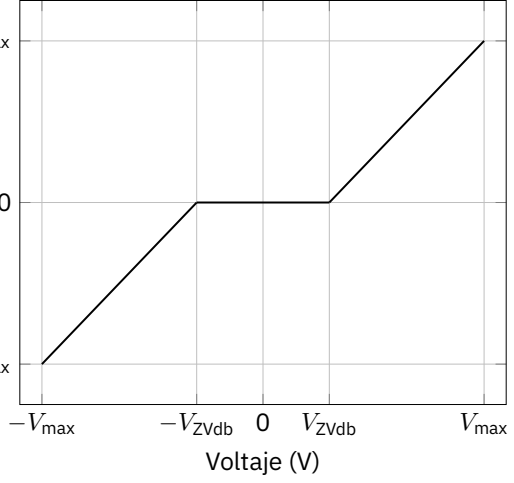
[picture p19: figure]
Vmax; VZVdb; Voltaje (V)

## omax0 omax

Posición o velocidad objetivo

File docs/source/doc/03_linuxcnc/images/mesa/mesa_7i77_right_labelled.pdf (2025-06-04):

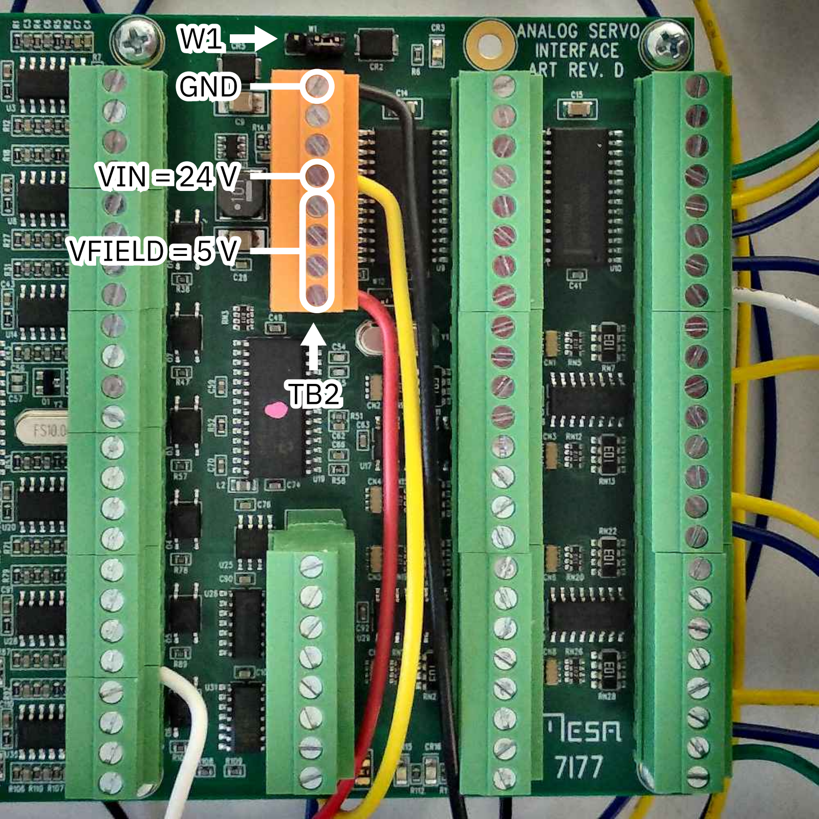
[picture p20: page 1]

W1

TB2

GND

VIN = 24 V

VFIELD = 5 V

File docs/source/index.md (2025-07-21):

# {{project}}

A motor control testbed using the open-source [LinuxCNC](https://www.linuxcnc.org) platform integrated with the [Mesa Electronics](https://store.mesanet.com/) 7i96S and 7I77 interface cards and the [igus® dryve D1](https://www.igus.eu/product/D1) motor controllers.

This system was used to develop and validate the control system for [a large high-precision 3-axis gantry robot system](https://github.com/GTEC-UDC/linuxcnc_gantry_robot).

---

Copyright (C) 2000-2022 LinuxCNC.org\
Copyright (C) 2025 Tomás Domínguez Bolaño, Valentín Barral Vales, Carlos José Escudero Cascón, and José Antonio García Naya.

Permission is granted to copy, distribute and/or modify this document
under the terms of the GNU Free Documentation License, Version 1.3
or any later version published by the Free Software Foundation;
with no Invariant Sections, no Front-Cover Texts, and no Back-Cover Texts.
A copy of the license is included in the section entitled "GNU Free Documentation License".

---

This work has been supported by grant PID2022-137099NB-C42 (MADDIE) and by project TED2021-130240B-I00 (IVRY) funded by MCIN/AEI/10.13039/501100011033 and the European Union NextGenerationEU/PRTR.

:::{ext-image} images/logos/ack_logos.*
:width-html: 700px
:name: fig:ack_logos
:::

:::{only} html
<!-- -->
---
<!-- -->
:::

:::{toctree}
:maxdepth: 2
:numbered:
:caption: Table of Contents

doc/01_introduction/introduction.md
doc/02_igus_dryve_d1/00_index.md
doc/03_linuxcnc/00_index.md
:::

:::{raw} latex
% Do not show section numbers for the following sections in latex
\setcounter{secnumdepth}{-1}
:::

:::{toctree}
:maxdepth: 1

fdl-1.3.md
bibliography.md
:::

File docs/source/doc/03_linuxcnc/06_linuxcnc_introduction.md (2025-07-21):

# Introduction to LinuxCNC

LinuxCNC is a highly customizable suite of applications for controlling {{CNC}} machines, 3D printers, robots, and other automated devices. It is capable of providing coordinated control of up to nine axes of motion. LinuxCNC comprises several key components integrated into a complete system {cite}`linuxcncdoc`:

- A {{GUI}}, which serves as the primary interface between the operator, the software, and the {{CNC}} machine itself.
- The {{HAL}}, which enables the linking of signals from the external environment with LinuxCNC and vice versa.
- High-level modules that coordinate the generation, execution, and motion control of the {{CNC}} machine, specifically the motion controller, the input/output controller, and the task executor.

This document provides only a brief overview of LinuxCNC; for more detailed information, it is recommended to consult the LinuxCNC user manual {cite}`linuxcncdoc`, which comprehensively describes how to use the software. On a system with LinuxCNC installed, the manual can be accessed by clicking on {menuselection}`Applications menu --> CNC --> Documentation`.

## Running LinuxCNC

You can run LinuxCNC by clicking on {menuselection}`Applications menu --> CNC --> LinuxCNC` or by using the `linuxcnc` command. Its usage is shown in {numref}`lst:linuxcnc_help`.

:::{code-block} text
:name: lst:linuxcnc_help
:caption: Usage of the linuxcnc command

linuxcnc: Run LinuxCNC

Usage:
  $ linuxcnc -h
    This help

  $ linuxcnc [Options]
    Choose the configuration INI file graphically

  $ linuxcnc [Options] path/to/your_ini_file
    Name the configuration INI file using its path

  $ linuxcnc [Options] -l
    Use the previously used configuration INI file

Options:
    -d: Turn on "debug" mode
    -v: Turn on "verbose" mode
    -r: Disable redirection of stdout and stderr to ~/linuxcnc_print.txt and
        ~/linuxcnc_debug.txt when stdin is not a tty.
        Used when running linuxcnc tests non-interactively.
    -l: Use the last-used INI file
    -k: Continue in the presence of errors in HAL files
    -t "tpmodulename [parameters]"
            specify custom trajectory_planning_module
            overrides optional INI setting [TRAJ]TPMOD
    -m "homemodulename [parameters]"
            specify custom homing_module
            overrides optional INI setting [EMCMOT]HOMEMOD
    -H "dirname": search dirname for HAL files before searching
                  INI directory and system library:
                  /home/git/linuxcnc-dev/lib/hallib
Note:
    The -H "dirname" option may be specified multiple times
:::

If you click on {menuselection}`Applications menu --> CNC --> LinuxCNC` or run the `linuxcnc` command without specifying a configuration file, the LinuxCNC configuration selector will open, as shown in {numref}`fig:linuxcnc_conf_selector`.

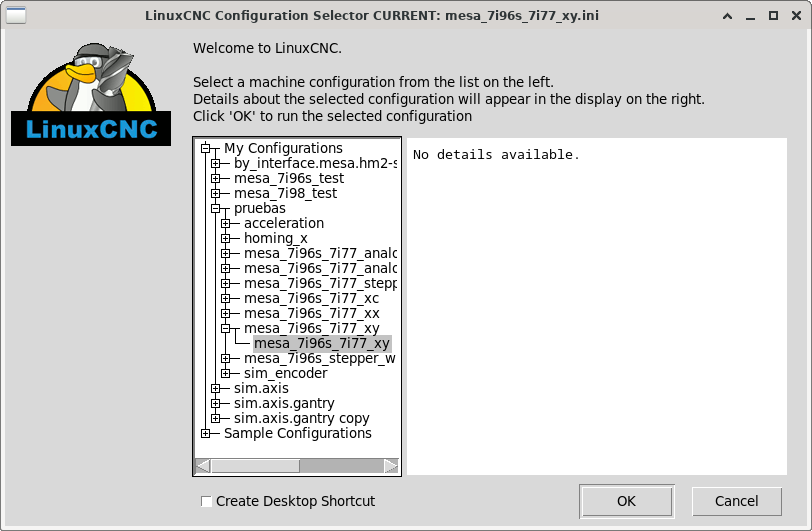
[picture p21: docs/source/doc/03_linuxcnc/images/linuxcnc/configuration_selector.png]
:::{figure} images/linuxcnc/configuration_selector.png
:name: fig:linuxcnc_conf_selector

LinuxCNC configuration selector.
:::

In the configuration selector, available configurations are displayed in a tree structure, reflecting their directory structure, with two initial nodes:

- **My configurations**: User-defined configurations, stored in the `~/linuxcnc/configs` folder.
- **Sample configurations**: Example configurations provided by default with LinuxCNC, stored in `/usr/share/linuxcnc/configs`.

To start LinuxCNC with a configuration, simply double-click on it or select it and press the {guilabel}`OK` button.
If you check the "Create Desktop Shortcut" box, a desktop icon will also be created to directly launch LinuxCNC with the respective configuration. Finally, if the configuration is one of the *Sample configurations*, LinuxCNC will prompt the user to copy it to the `~/linuxcnc/configs` folder, allowing for later modification. If the user accepts, the configuration will subsequently appear under the *My configurations* category.

(sec:linuxcnc_intro_config)=
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

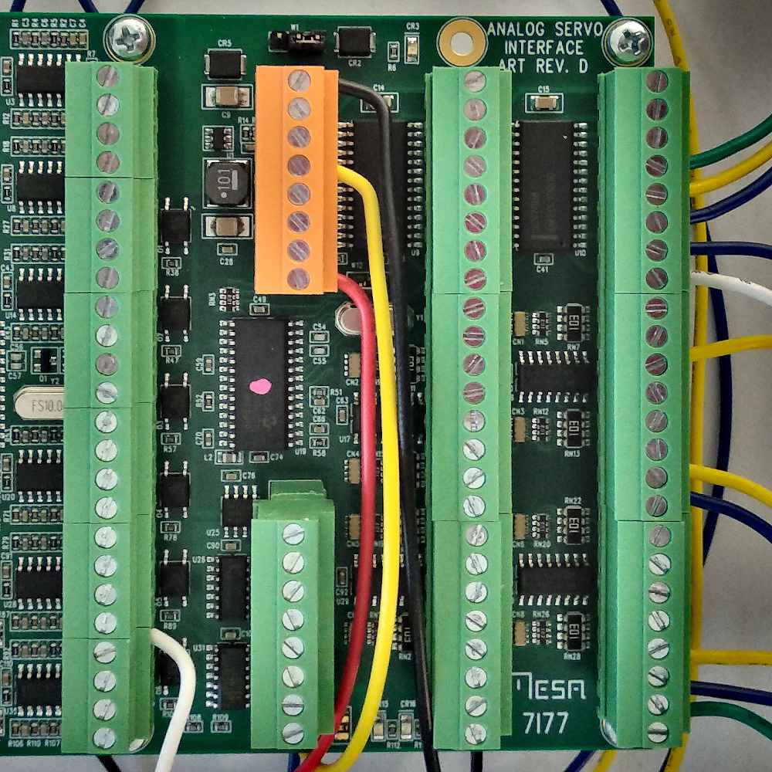
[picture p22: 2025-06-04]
docs/source/doc/03_linuxcnc/images/mesa/mesa_7i77_right.jpg

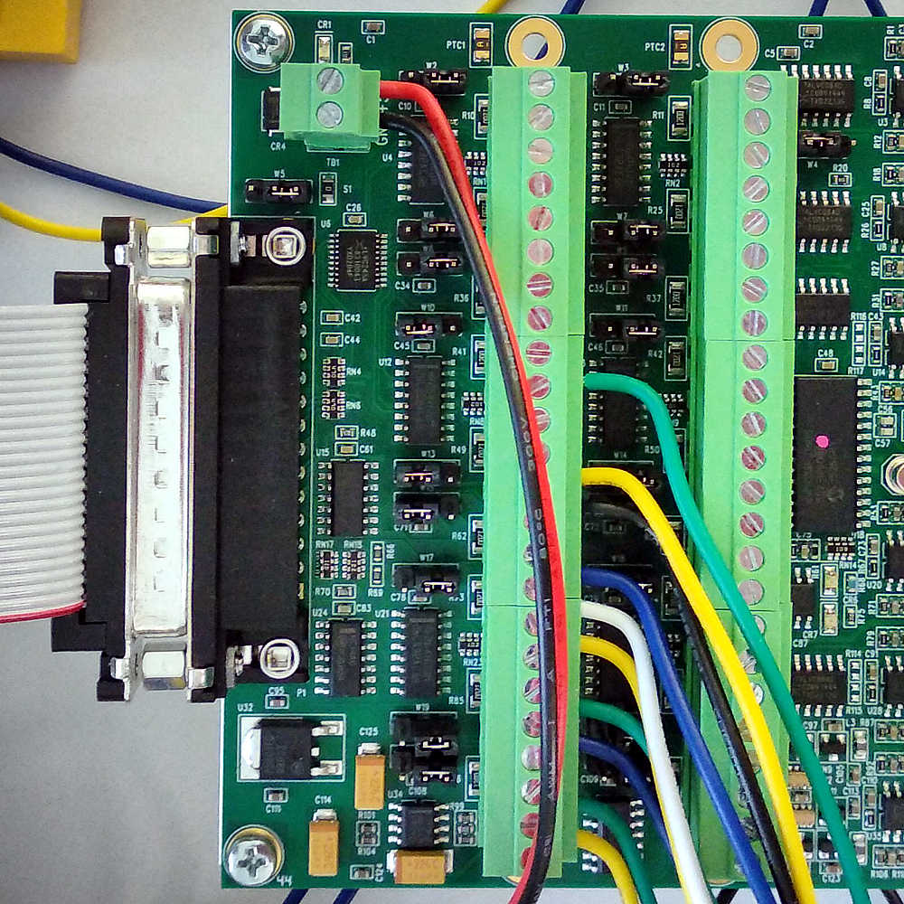
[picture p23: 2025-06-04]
docs/source/doc/03_linuxcnc/images/mesa/mesa_7i77_left.jpg

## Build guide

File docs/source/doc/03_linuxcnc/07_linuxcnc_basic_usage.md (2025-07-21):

---
myst:
  substitutions:
    button_estop: "button_estop"
    button_on_disabled: "button_on_disabled"
    button_on: "button_on"
    button_run: "button_run"
    homed_symbol: "homed_symbol"
---

(sec:linuxcnc_usage)=
# Basic LinuxCNC Usage

During the development of the testbed, three LinuxCNC configurations were created:

- `mesa_7i96s_7i77_xy`: Simulates a robot with X and Y axes, where the brushless motor controls the X-axis and the stepper motor controls the Y-axis.
- `mesa_7i96s_7i77_xx`: Simulates a robot with a single X-axis, where both the brushless and stepper motors control the axis simultaneously, moving synchronously at the same speed.
- `mesa_7i96s_7i77_xc`: Simulates a robot with an X-axis and a C-axis (rotation around the Z-axis). The brushless motor controls the X-axis, and the stepper motor controls the C-axis.

The following sections explain how to use LinuxCNC with these configurations.

(sec:linuxcnc_usage_gui_axis)=
## Control using the AXIS Graphical Interface

When LinuxCNC is launched with one of the aforementioned configurations, the AXIS graphical interface will open, as shown in {numref}`fig:linuxcnc_gui_axis_estop`. The process for controlling the machine with this interface is detailed below.

### Setting LinuxCNC to the "ON" State

The initial state of LinuxCNC will be "ESTOP" (emergency stop), indicated at the bottom left of the window, thus disabling robot movement. To start the robot, you must first clear the "ESTOP" condition. To do this, proceed as follows:

1. Deactivate the physical emergency stop switch (see {numref}`fig:installation`). If this switch is active, it forces the emergency stop state in LinuxCNC.
2. Deactivate the emergency stop state in LinuxCNC by pressing the {{button_estop}} button.

Once the emergency stop state is deactivated, LinuxCNC will transition to the "OFF" state, and the start button will change from a deactivated state ({{button_on_disabled}}) to an activated state ({{button_on}}).
To begin using the robot, press this button, which will transition LinuxCNC to the "ON" state. {numref}`fig:linuxcnc_gui_axis_on` shows the AXIS interface in the "ON" state.

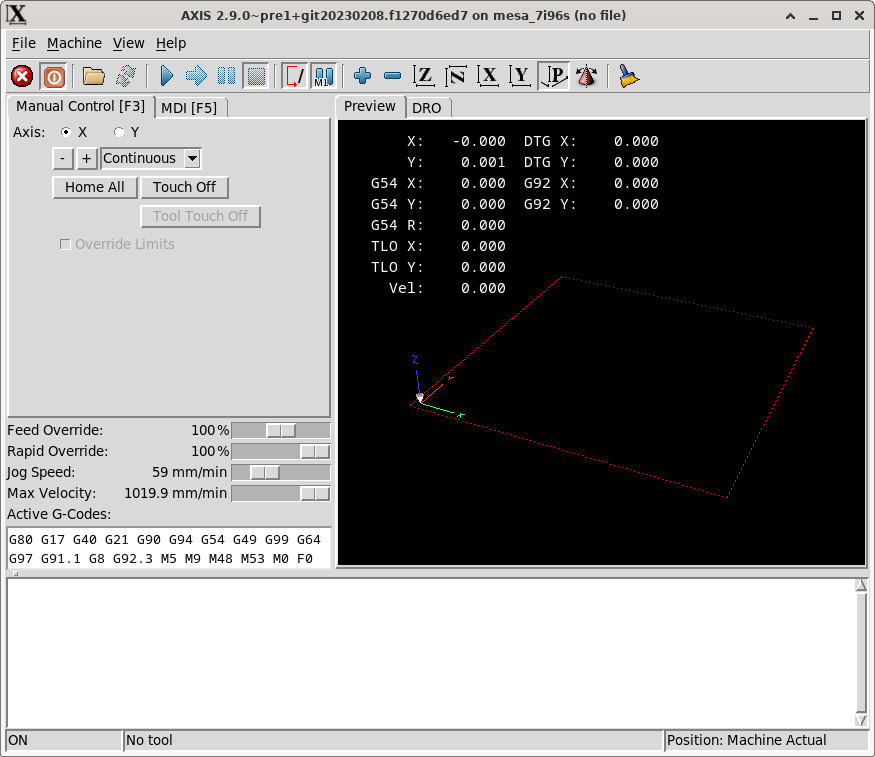
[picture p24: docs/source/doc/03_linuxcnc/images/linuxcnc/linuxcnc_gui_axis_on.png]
:::{figure} images/linuxcnc/linuxcnc_gui_axis_on.png
:name: fig:linuxcnc_gui_axis_on

LinuxCNC "AXIS" graphical interface in "ON" state.
:::

### Homing the Machine

Once LinuxCNC is in the "ON" state, you can manually control the machine using the {guilabel}`-` and {guilabel}`+` controls on the "Manual Control" tab. However, to execute specific G-code positioning commands (e.g., moving the machine to X=1, Y=5), it is necessary to perform the homing process. The homing procedure involves establishing a precise reference point for all machine axes, providing LinuxCNC with exact knowledge of the machine's current position.

To perform the homing process, you can click the {guilabel}`Home All` button on the "Manual Control" tab or select the menu entry {menuselection}`Machine --> Homing --> Home all axes`. In the testbed configurations, the homing process uses a single limit switch per motor. The procedure LinuxCNC follows for homing with limit switches is as follows:

1. Move the motor towards the limit switch until it is activated.
2. Move the motor in the opposite direction until the limit switch is deactivated.
3. Move the motor again towards the limit switch until it is activated, this time at a slower speed to precisely locate the switch's position.
4. Move the motor to the designated home reference position.

In the `mesa_7i96s_7i77_xy` and `mesa_7i96s_7i77_xx` configurations, you must manually activate the limit switches for both motors. In the `mesa_7i96s_7i77_xc` configuration, only the brushless motor's limit switch needs manual activation; the stepper motor in this case uses a different homing process that simply seeks the encoder's index pulse position.

{numref}`fig:linuxcnc_gui_axis_on_homed` shows the interface window after the homing process is complete. The {{homed_symbol}} symbol can now be seen next to the X and Y axis information in the display area, indicating that the axes are homed.

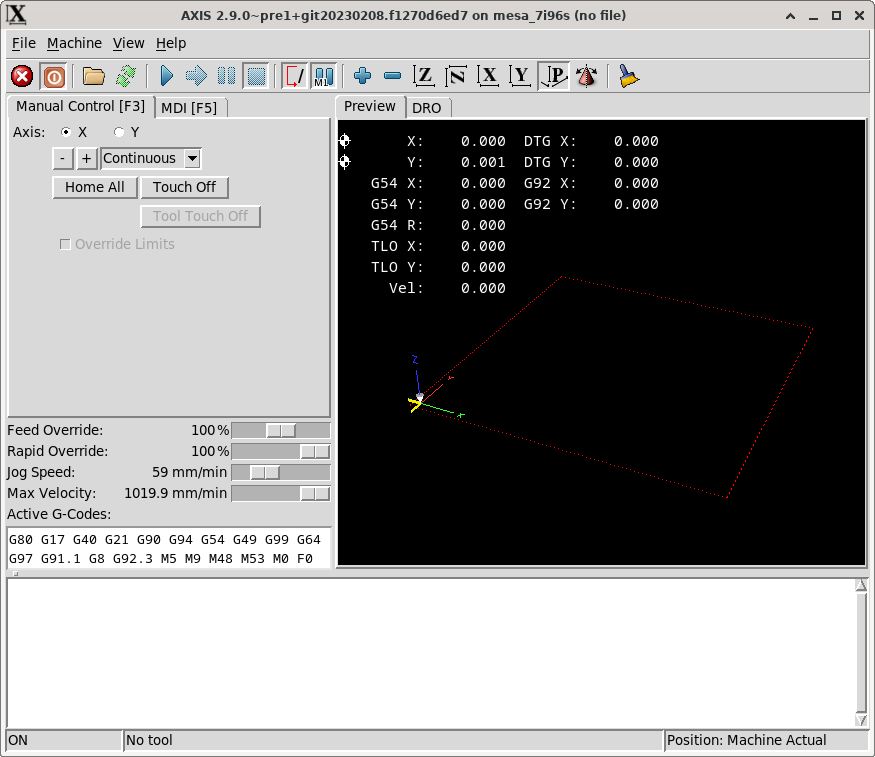
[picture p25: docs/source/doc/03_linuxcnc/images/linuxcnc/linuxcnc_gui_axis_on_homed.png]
:::{figure} images/linuxcnc/linuxcnc_gui_axis_on_homed.png
:name: fig:linuxcnc_gui_axis_on_homed

LinuxCNC "AXIS" graphical interface in "ON" state with all axes homed.
:::

### Controlling the Machine

As mentioned in {numref}`sec:linuxcnc_modes_of_operation`, LinuxCNC offers three control modes: manual, MDI, and automatic. The AXIS interface allows controlling the machine using these modes as follows:

- **Manual mode**: You can control the machine manually via the {guilabel}`-` and {guilabel}`+` controls on the "Manual Control" tab.
- **MDI mode**: You can use MDI mode via the "MDI" tab, where G-code commands can be entered line by line.
- **Automatic mode**: You can load a G-code program from a file by clicking on {menuselection}`File --> Open` and then execute it in automatic mode by clicking the {{button_run}} button or pressing the {kbd}`R` key.

For more information on G-code control, consult the "G-code programming" section in the LinuxCNC manual {cite}`linuxcncdoc`.

## Programmatic Control

LinuxCNC can be controlled programmatically by including a sequence of instructions in two ways:

1. Using G-code programs stored in a file, as mentioned in the previous section.
2. Using Python programs with the `linuxcnc` library, which is included with LinuxCNC and allows interaction with the running LinuxCNC process. For more information, consult the "Python Interface" section in the LinuxCNC user manual. {numref}`lst:linuxcnc_python` provides an example of robot control using Python by sending G-code commands in MDI mode.

:::{code-block} python
:name: lst:linuxcnc_python
:caption: Example of using Python to interact with LinuxCNC

#!/usr/bin/env python3
# Example of LinuxCNC control with Python
# See the LinucCNC user manual, section 13.5 - Python Interface

import sys
import linuxcnc

def control_robot(c: linuxcnc.command) -> None:
    def set_feed_rate(v: float):
        # set robot feed rate
        c.mdi(f"F{v}")
        c.wait_complete()

    def go_to(x: float, y: float):
        # go to position (x, y)
        print(f"Going to ({x}, {y})...", end="", flush=True)
        c.mdi(f"G1 X{x} Y{y}")
        while (ret := c.wait_complete(1)) == -1:
            continue
        print(" done")
        if ret == linuxcnc.RCS_ERROR:
            print("RCS_ERROR")

    # Put your robot commands here
    set_feed_rate(400)
    go_to(0, 0)

def main():
    s = linuxcnc.stat()  # connect to the status channel
    c = linuxcnc.command()  # connect to the command channel

    def ok_for_mdi() -> bool:
        s.poll()
        return (
            not s.estop
            and s.enabled
            and (s.homed.count(1) == s.joints)
            and (s.interp_state == linuxcnc.INTERP_IDLE)
        )

    if ok_for_mdi():
        c.mode(linuxcnc.MODE_MDI)
        c.wait_complete()  # wait until mode switch executed
        print("OK, running...")
        try:
            control_robot(c)
        except KeyboardInterrupt:
            c.abort()
            sys.exit(1)
    else:
        print("Not OK for running. Check that the robot is homed and idle.")
        sys.exit(1)

if __name__ == "__main__":
    try:
        main()
    except linuxcnc.error as e:
        print("error: ", e)
        print("is LinuxCNC running?")
        sys.exit(1)
:::

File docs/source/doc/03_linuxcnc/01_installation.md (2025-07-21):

(sec:linuxcnc_installation)=
# Installation

LinuxCNC is available for installation from the official repositories of Debian and Ubuntu distributions. For our testbed setup, we installed Debian 12 with the XFCE desktop environment. Once the operating system is installed, follow these steps to install LinuxCNC:

1. Update the system's package index by running the following commands:

    ```sh
    sudo apt-get update sudo apt-get dist-upgrade
    ```

2. Install LinuxCNC using the following command:

    ```sh
    sudo apt-get install linuxcnc-uspace linuxcnc-uspace-dev
    ```

    LinuxCNC requires a real-time Linux kernel. The `linuxcnc-uspace` package includes `linux-image-amd64` as a dependency, which provides the Linux kernel with `PREEMPT_RT` patches to convert it into a real-time system.

3. Install `mesaflash`, the MESA board configuration and diagnostic tool, using the following command:

    ```sh
    sudo apt-get install mesaflash
    ```

4. Restart the system. After restarting, the system should be using the real-time kernel. To verify the kernel version in use, run the following command:

    ```sh
    uname -v
    ```

    The output should specify the `PREEMPT_RT` kernel version, similar to the example below:

    ```text
    #1 SMP PREEMPT_RT Fri Oct 6 19:02:35 UTC 2023
    ```

5. Optionally, you can uninstall the standard Linux kernel with the following command:

    ```sh
    sudo apt-get remove linux-image-amd64
    ```

Once the LinuxCNC package is installed, a "CNC" entry will appear in the applications menu, which will contain the following items:

- **Documentation**: LinuxCNC documentation in PDF format, including the user manual and man pages.
- **G-code Quick-Reference**: A quick reference page for G-code commands.
- **Latency Histogram**: Display a latency histogram.
- **Latency Test**: Run a latency test to determine the maximum system latency or jitter.
- **LinuxCNC**: The LinuxCNC launcher, allowing you to select the LinuxCNC configuration to execute.
- **Pncconf wizard**: A wizard for generating LinuxCNC configurations that use MESA boards.
- **Stepconf wizard**: A wizard for generating LinuxCNC configurations that use the parallel port to control stepper motors.

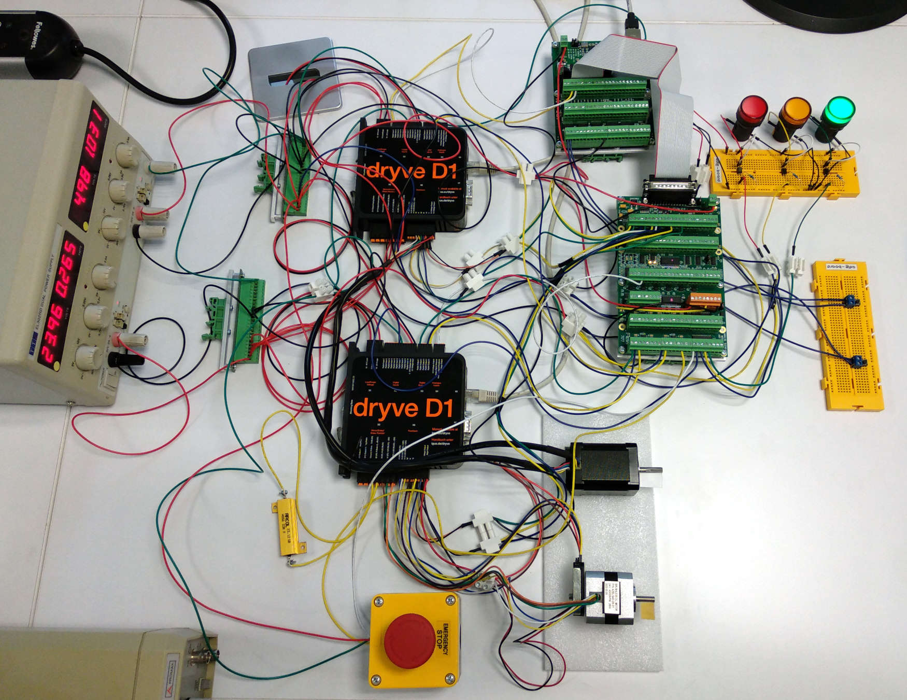
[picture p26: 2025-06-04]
docs/source/doc/01_introduction/images/installation.jpg

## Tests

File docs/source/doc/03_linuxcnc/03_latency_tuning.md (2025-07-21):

# System Latency Tuning

The maximum system latency can depend on various factors such as hardware, firmware configuration, system load, and hardware interrupt handling. If the maximum system latency is too high, adjustments to the system configuration will be necessary to reduce it. Various sources, including official documentation, guides, and talks, provide detailed guidelines for optimizing the performance of real-time Linux systems {cite}`redhat_rt_low_latency,ubuntu_rt_tuning,lfoss2022tips,elc2023preparing`. The LinuxCNC user manual {cite}`linuxcncdoc` also suggests several potential adjustments to reduce latency, which are detailed in the following sections.

For our testbed setup, we used a Lenovo T430s laptop equipped with an Intel Core i5-3320M CPU and running Debian 12. Additionally, we only considered the use of a slow thread with a 1 ms period. In this case, the latency values obtained, as shown in Figures {numref}`%s <fig:linuxcnc_latency_plot>`, {numref}`%s <fig:linuxcnc_latency_test>`, and {numref}`%s <fig:linuxcnc_latency_histogram>`, were sufficiently low without requiring any further modifications. However, note that for other hardware, even with the same operating system, the latency values could be higher. If the system latency becomes too high during LinuxCNC operation, a warning similar to {numref}`fig:linuxcnc_gui_axis_delay_warning` would appear.

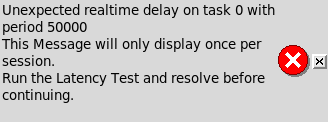
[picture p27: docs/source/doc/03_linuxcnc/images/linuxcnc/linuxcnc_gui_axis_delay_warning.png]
:::{figure} images/linuxcnc/linuxcnc_gui_axis_delay_warning.png
:name: fig:linuxcnc_gui_axis_delay_warning

LinuxCNC warning for unexpected latency values.
:::

## Firmware Settings

System firmware such as the {{BIOS}} or {{UEFI}}, can significantly impact system latency. This impact varies depending on the hardware manufacturer and the quality of the provided firmware. Firmware is responsible for initializing and configuring system hardware before the operating system loads. If the firmware is not properly configured to provide accurate timing or does not adequately manage interrupts and hardware devices, it can contribute to increased system latency.

The firmware settings recommended in the LinuxCNC user manual {cite}`linuxcncdoc` that can help reduce latency include the following:

- Disable {{APM}}, {{ACPI}}, and other power-saving functions, including all suspension related features and CPU frequency scaling.
- Disable CPU "turbo" mode.
- Disable CPU simultaneous multithreading technology, e.g., Intel's Hyper-Threading technology.
- Disable or limit SMIs (System Management Interrupts).
- Disable unused hardware.

## Linux Settings

Linux offers various options that can help improve latency. Specifically, for our case, we will consider kernel boot command-line parameters and runtime parameters configured via the `sysctl` command. These parameters are described below.

### Kernel Boot Command-Line Parameters

A comprehensive list of parameters is available at <https://docs.kernel.org/admin-guide/kernel-parameters.html>. In Debian, command-line parameters can be specified in the following ways:

1. In the GRUB bootloader, you can press a key (often `e`) to edit the selected boot entry and append the parameters to the end of the line. Once added, you can boot the system by pressing `F10` or `Ctrl+X`.
2. To persistently specify parameters, edit the `/etc/default/grub` file, adding the parameters to the `GRUB_CMDLINE_LINUX_DEFAULT` variable, and then run the `update-grub` command. For more information about GRUB configuration variables, refer to the corresponding manual page at <https://www.gnu.org/software/grub/manual/grub/html_node/Simple-configuration.html>.

For latency optimization, the most relevant parameters, as suggested in the LinuxCNC user manual {cite}`linuxcncdoc`, are:

- `isolcpus`: A list of CPUs that will be isolated from balancing and scheduling algorithms. This prevents most system processes from using the specified CPUs, thereby making more CPU time available for LinuxCNC.
- `irqaffinity`: A list of CPUs to set as the default IRQ affinity mask. This selects the CPUs that will handle interrupts, ensuring that the remaining CPUs do not have to perform this task.
- `rcu_nocbs`: A list of CPUs whose {{RCU}} callbacks will be executed on other CPUs.{cite}`enwiki:1169786538,redhat_rt_rcu`.
- `rcu_nocb_poll`: This option periodically wakes up {{RCU}} callback execution threads using a timer to check for callbacks to execute. Without this option, the CPUs specified in `rcu_nocbs` are responsible for waking up the threads that execute {{RCU}} callbacks {cite}`redhat_rt_rcu`. This option improves the real-time responsiveness of the CPUs listed in `rcu_nocbs` by freeing them from the need to wake up their corresponding threads.
- `nohz_full`: A list of CPUs that will cease receiving timing ticks when only one task is executing. As a result, these CPUs can dedicate more time to executing applications and less time to handling interrupts and context switching. The CPUs in this list will have their {{RCU}} callbacks transferred to other CPUs, as if they had been specified with the `rcu_nocbs` option.

To determine the number of processors in your system, you can use either the `nproc` command or `cat /proc/cpuinfo`. For instance, in a system with 4 CPUs, if you wish to isolate 3 CPUs from disturbances, you can use the following parameters:

```text
isolcpus=1-3 nohz_full=1-3 rcu_nocb_poll irqaffinity=0
```

### Runtime Parameters using `sysctl`

The `sysctl` command is used to modify kernel parameters at runtime. The available parameters are those listed in `/proc/sys/`. For latency, the LinuxCNC user manual {cite}`linuxcncdoc` suggests the following parameter:

- `sysctl.kernel.sched_rt_runtime_us`: This sets a global limit on the maximum CPU time that real-time tasks can consume. Set to -1 to remove the time limit. More information about this parameter can be found at <https://www.kernel.org/doc/html/latest/scheduler/sched-rt-group.html>.

To persistently set these parameters, they must be added to the `/etc/sysctl.conf` file or, preferably, to a new file within the `/etc/sysctl.d` directory. For more information, consult the `sysctl.conf` manual page.

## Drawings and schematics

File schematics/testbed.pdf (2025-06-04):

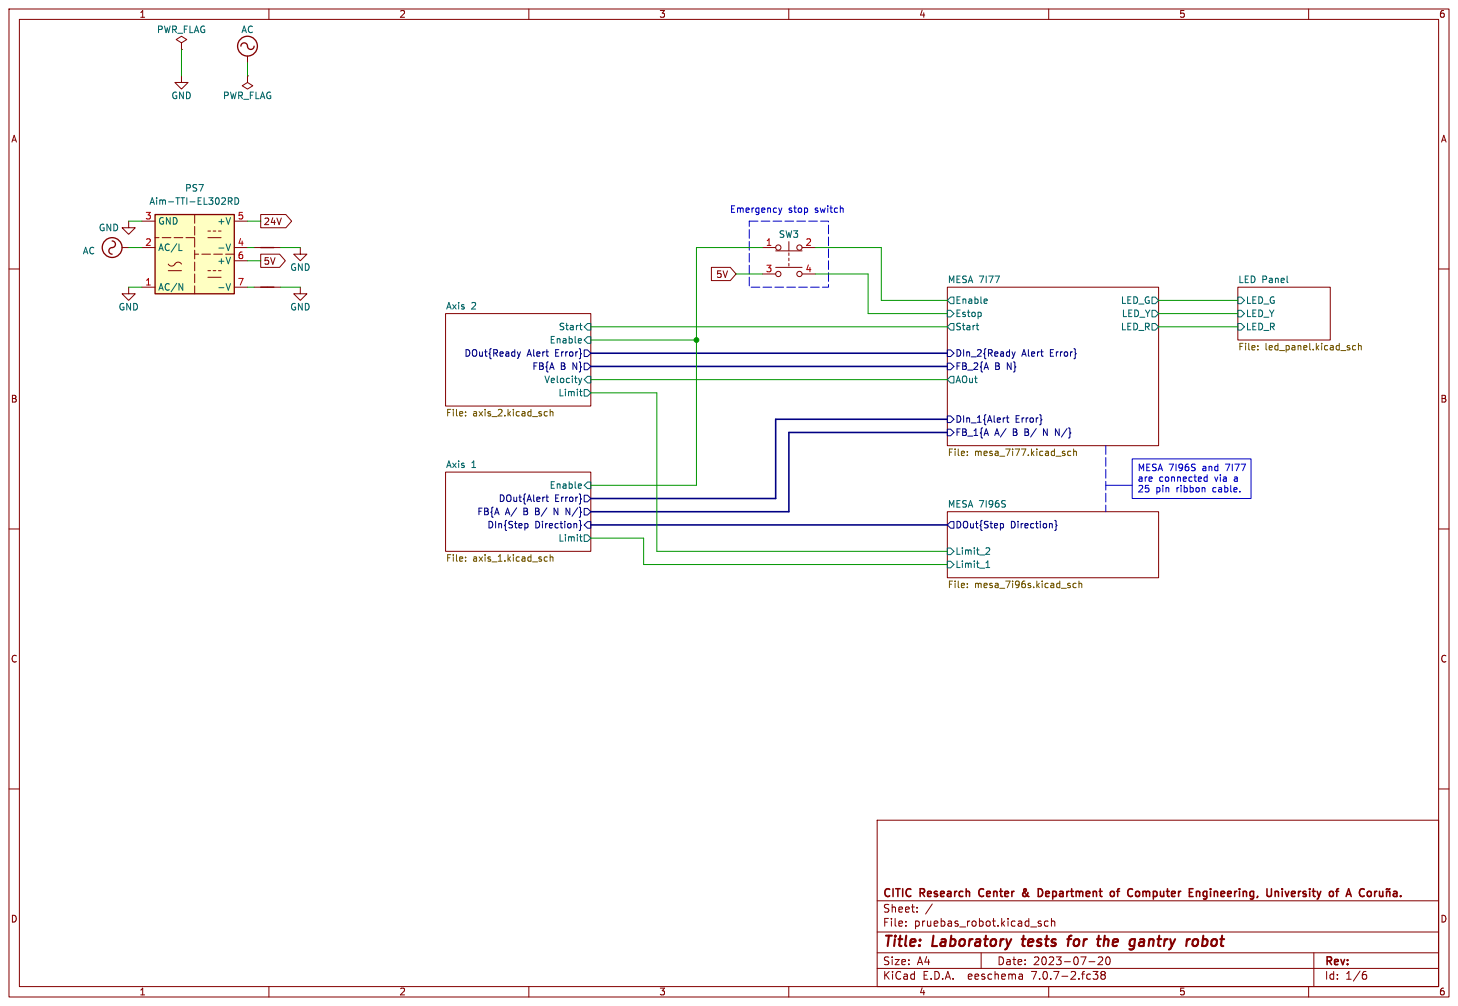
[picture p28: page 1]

Velocity Start Axis 2 File: axis_2.kicad_sch

Limit DOut{Ready Alert Error} Enable FB{A B N}

Limit_1 DOut{Step Direction} MESA 7I96S

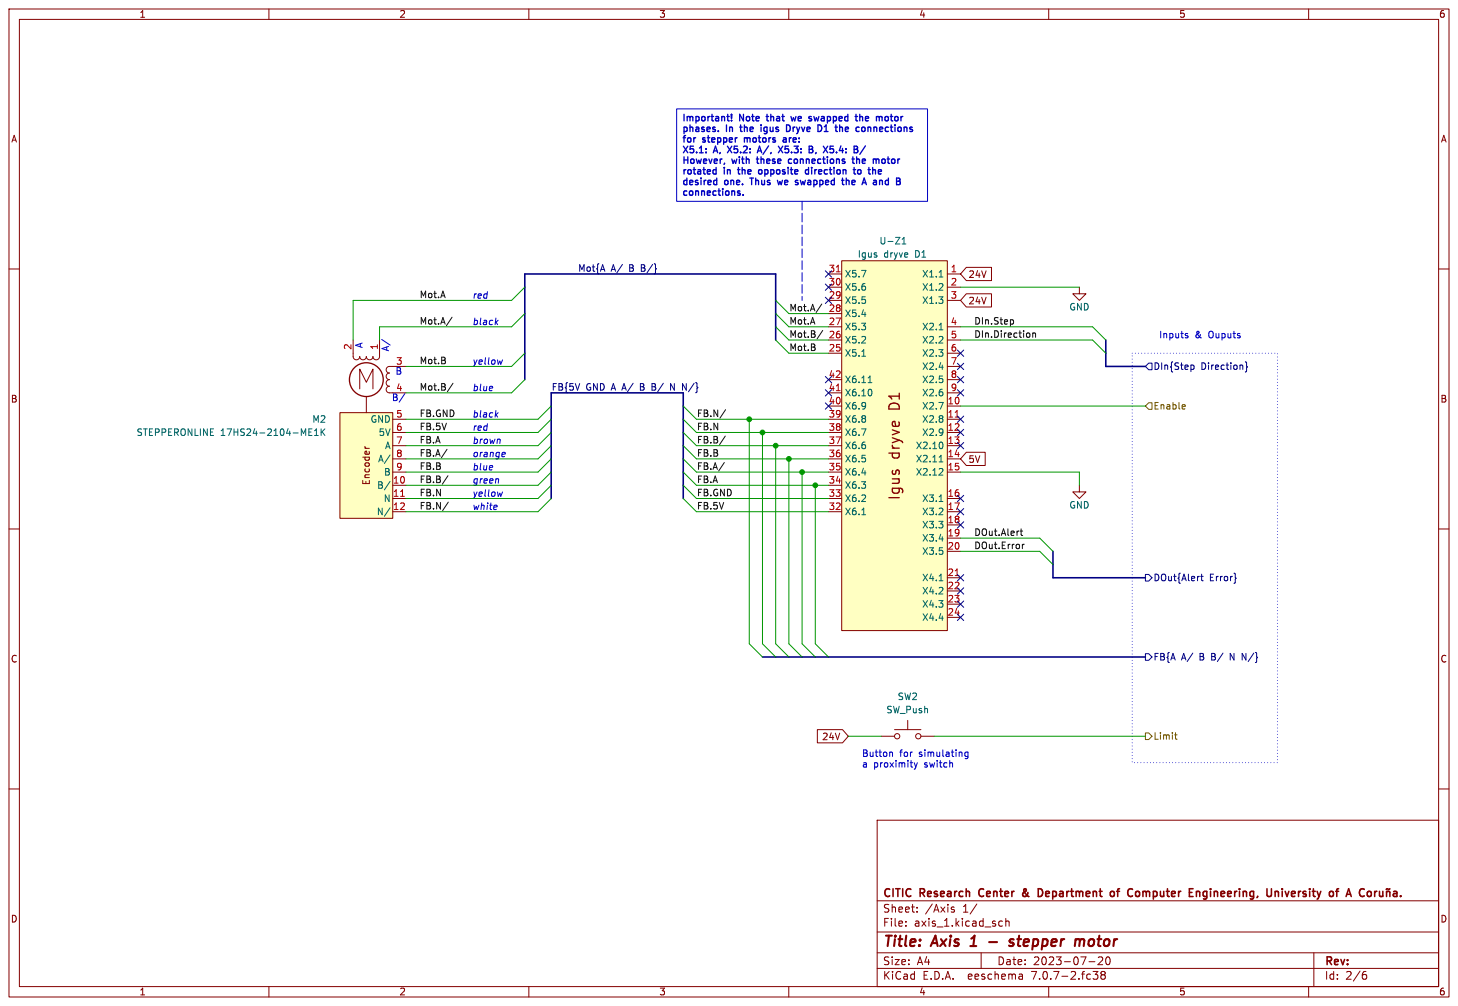
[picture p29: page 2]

Important! Note that we swapped the motor phases. In the igus Dryve D1 the connections

for stepper motors are: X5.1: A, X5.2: A/, X5.3: B, X5.4: B/ However, with these connections the motor

rotated in the opposite direction to the desired one. Thus we swapped the A and B

Inputs & Ouputs Button for simulating

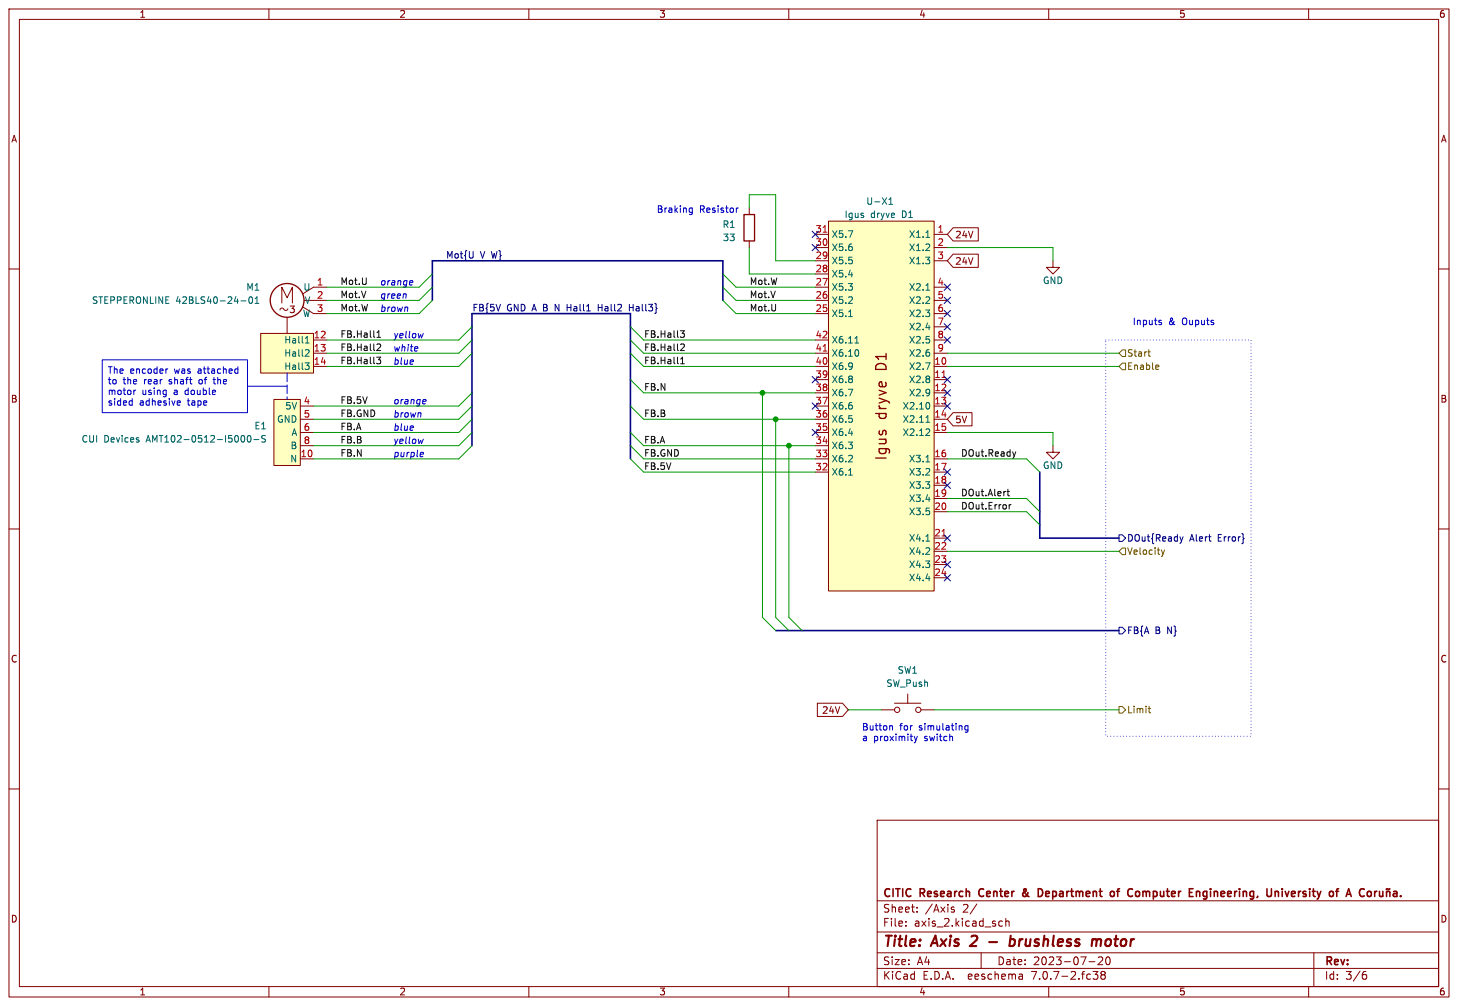
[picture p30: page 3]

brown The encoder was attached

DOut{Ready Alert Error} Limit Enable Start 5V

to the rear shaft of the motor using a double

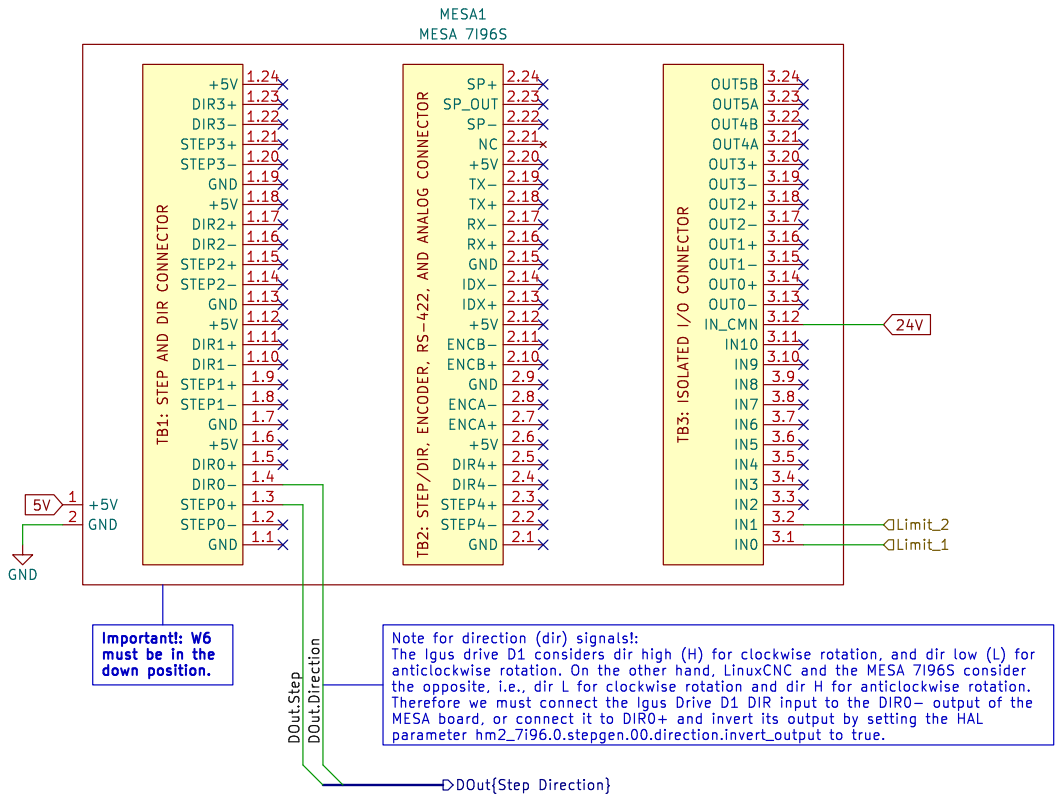
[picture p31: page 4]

Important!: W6 must be in the down position.

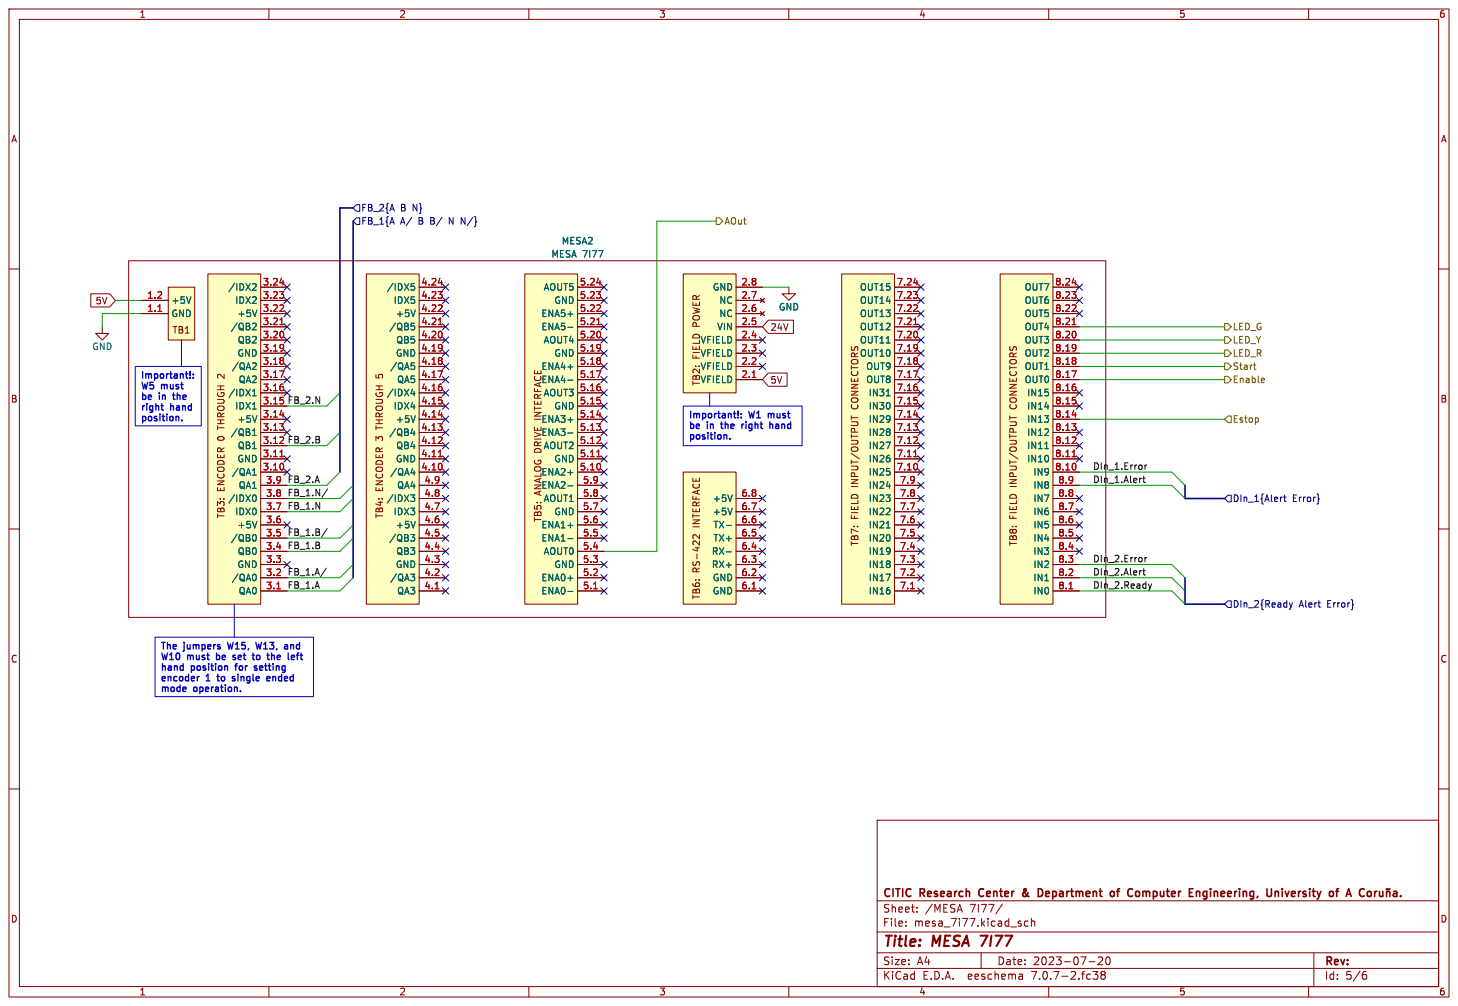
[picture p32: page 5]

Important!: W5 must be in the

encoder 1 to single ended mode operation.

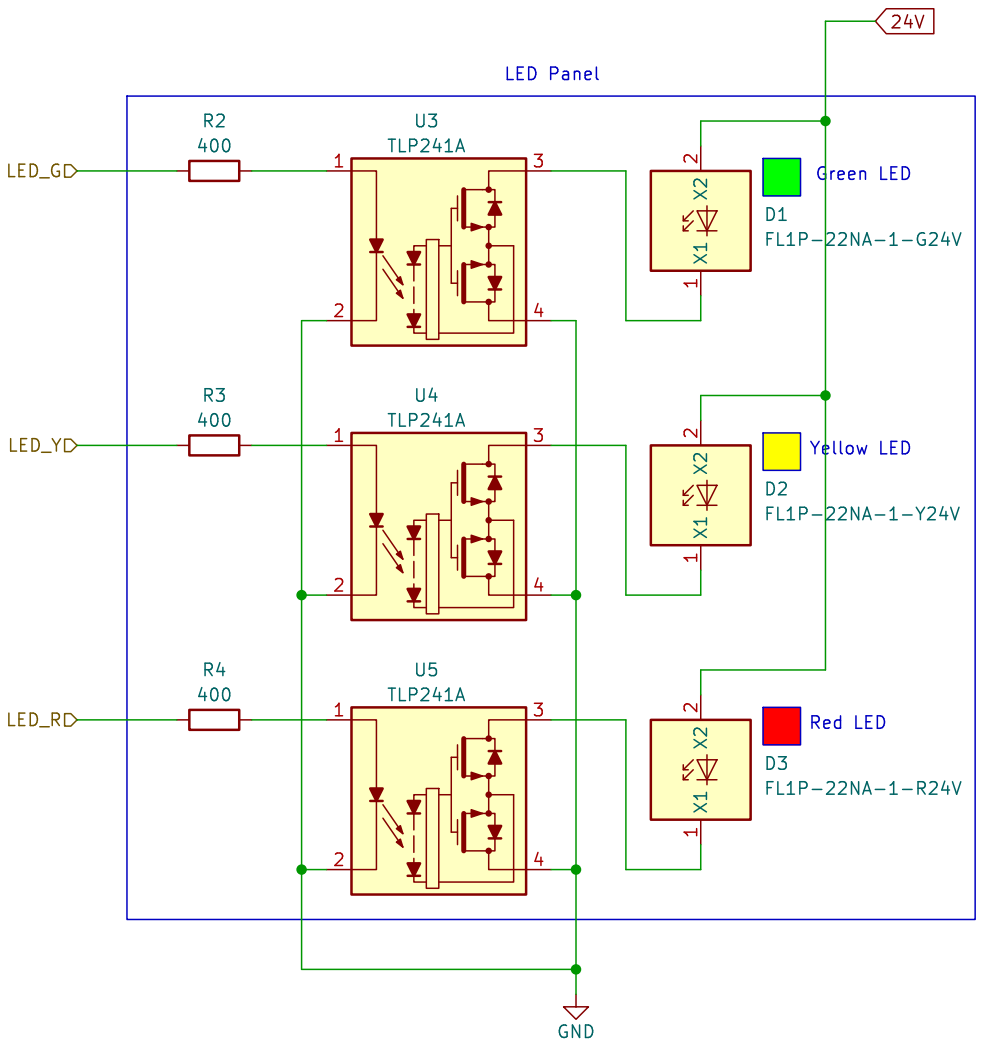
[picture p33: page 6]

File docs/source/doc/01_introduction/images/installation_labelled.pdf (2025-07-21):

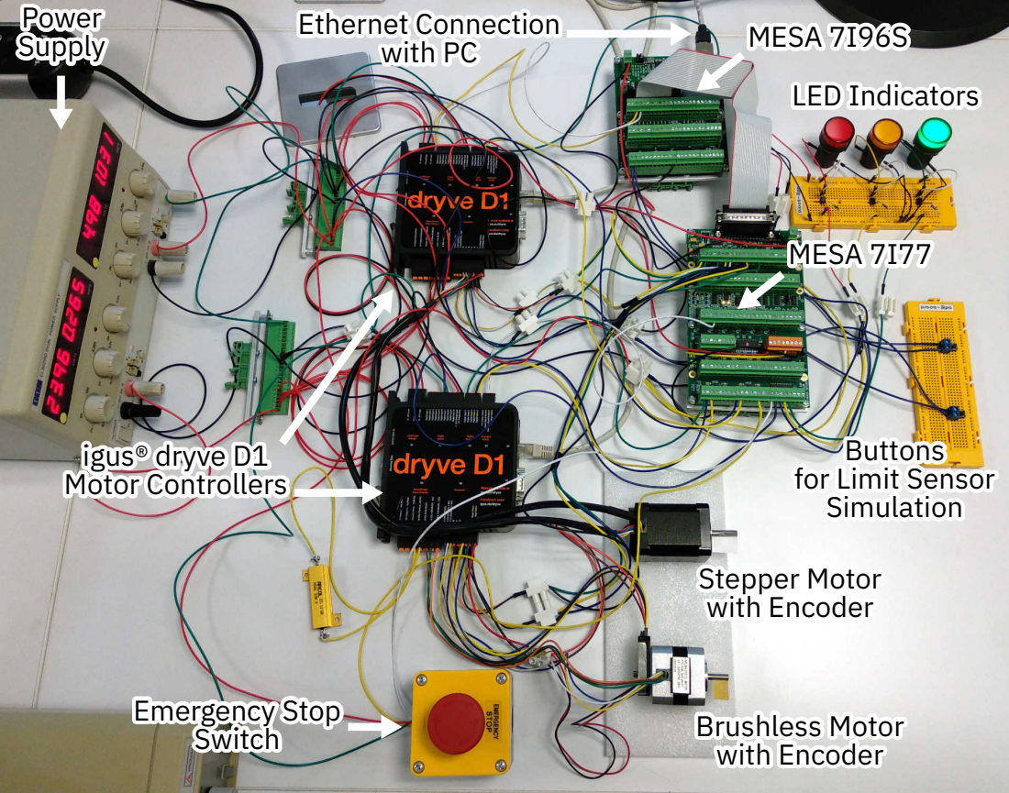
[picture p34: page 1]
MESA 7I96S; MESA 7I77; Stepper Motor with Encoder; Brushless Motor with Encoder; Emergency Stop Switch; LED Indicators; igus® dryve D1 Motor Controllers; Ethernet Connection with PC; Power Supply

Buttons
for Limit Sensor
Simulation

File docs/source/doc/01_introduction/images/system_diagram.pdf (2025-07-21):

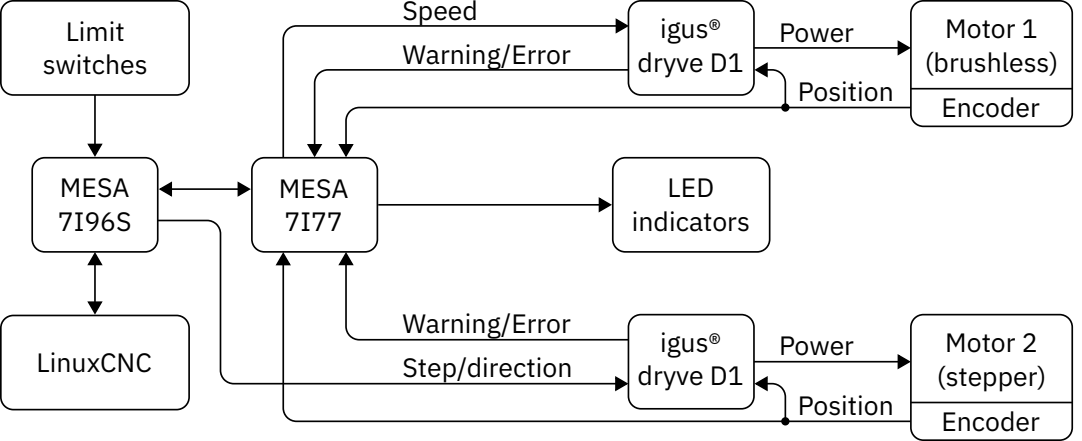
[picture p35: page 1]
Limit switches; MESA 7I96S; MESA 7I77; igus® dryve D1; Motor 1 (brushless) Encoder; Motor 2 (stepper) Encoder; Power; Position; Speed Warning/Error; Warning/Error; LinuxCNC; Step/direction; LED indicators

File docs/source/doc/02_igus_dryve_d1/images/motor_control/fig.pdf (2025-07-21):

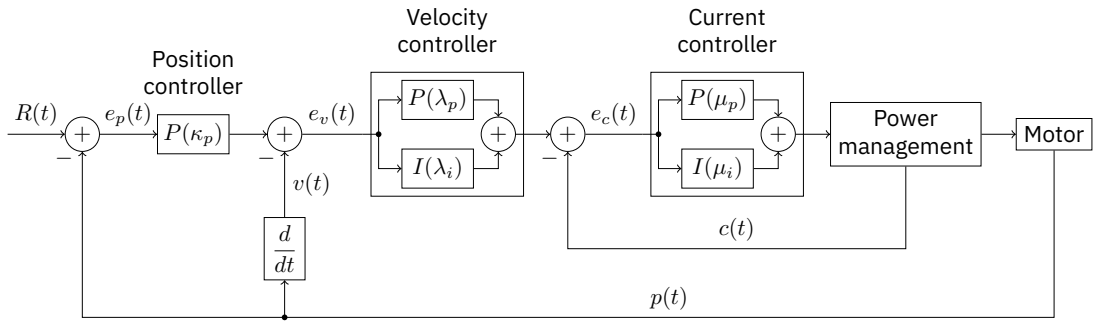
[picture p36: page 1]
Power; management; Motor; Position controller; Velocity controller; Current controller

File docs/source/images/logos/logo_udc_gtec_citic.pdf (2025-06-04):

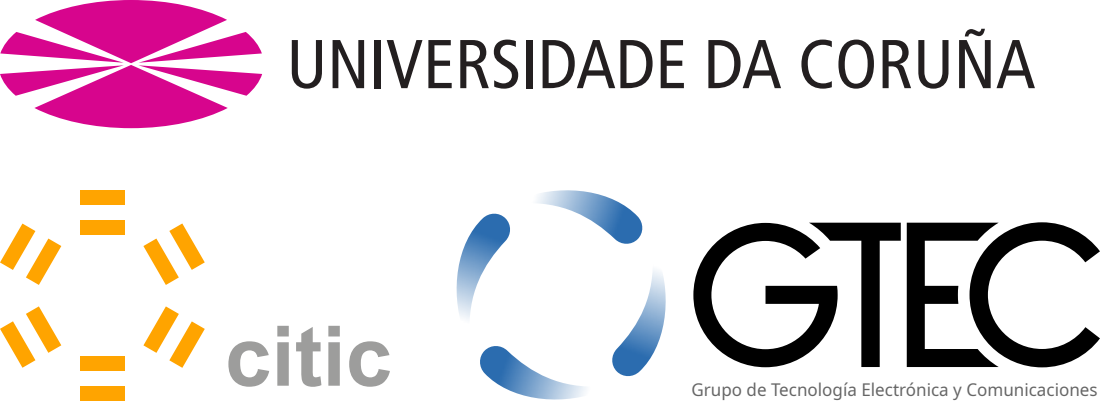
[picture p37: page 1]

Grupo de Tecnología Electrónica y Comunicaciones

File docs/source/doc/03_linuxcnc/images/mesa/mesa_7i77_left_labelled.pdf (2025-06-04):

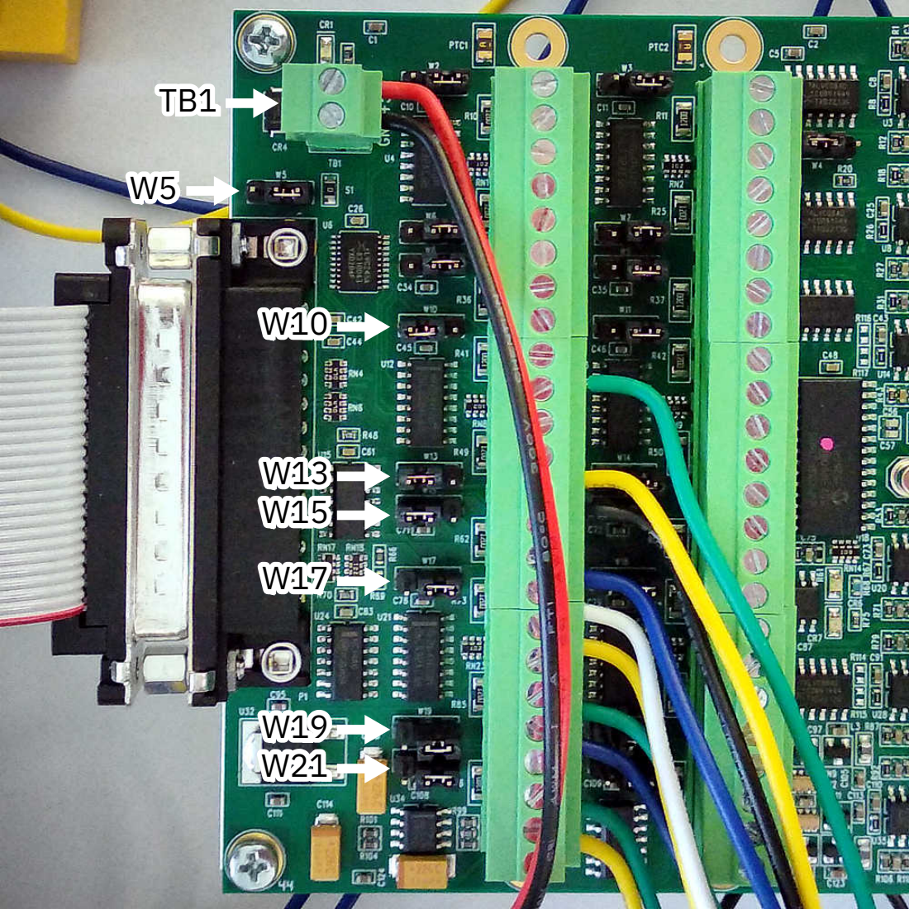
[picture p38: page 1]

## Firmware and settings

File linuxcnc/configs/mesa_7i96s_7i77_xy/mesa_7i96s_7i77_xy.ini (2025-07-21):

[EMC]
# General configuration

# Machine name, usually displayed in the interface window.
MACHINE = mesa_7i96s

# Debug flags, 0 means no debug messages will be printed.
DEBUG = 0

# Configuration version, for LinuxCNC 2.9 it should be 1.1.
VERSION = 1.1


[DISPLAY]
# Graphic interface configuration

# Type of graphic interface to use.
DISPLAY = axis

# Coordinate system: RELATIVE or MACHINE.
POSITION_OFFSET = MACHINE

# Coordinates to display: COMMANDED or ACTUAL.
POSITION_FEEDBACK = ACTUAL

# Maximum feed override. A feed override of 2 means
# 200% of the programmed feed rate.
MAX_FEED_OVERRIDE = 2.000000

# Image to display on the welcome screen.
INTRO_GRAPHIC = linuxcnc.gif

# Maximum welcome screen time in seconds.
INTRO_TIME = 5

# Default directory for G-code programs.
PROGRAM_PREFIX = /home/gtec/linuxcnc/nc_files

# Increments to move the robot with manual control.
INCREMENTS = 5mm 1mm .5mm .1mm .05mm .01mm .005mm

# The coordinate value that will be displayed: COMMANDED or ACTUAL
POSITION_FEEDBACK = ACTUAL

# Default linear velocity with manual control.
DEFAULT_LINEAR_VELOCITY = 1.000000

# Maximum linear velocity allowed with manual control.
MAX_LINEAR_VELOCITY = 10.000000

# Minimum linear velocity allowed with manual control.
MIN_LINEAR_VELOCITY = 0.000000

# Text editor to use when clicking on File -> Edit.
EDITOR = mousepad

# 3D view geometry of the preview window.
GEOMETRY = XY

# Update time in milliseconds.
CYCLE_TIME = 100

# File to open when starting LinuxCNC (optional).
OPEN_FILE = ""


[TASK]
# Task controller configuration

# Task controller module, milltask.
TASK = milltask

# Milltask execution period.
CYCLE_TIME = 0.010


[RS274NGC]
# RS274NGC interpreter configuration

# Interpreter variable file.
PARAMETER_FILE = linuxcnc.var

# Startup codes for the interpreter.
RS274NGC_STARTUP_CODE = G21 G40 G90 G94 G97 G64 P0.025


[EMCMOT]
# Motion controller configuration

# Motion controller module, motmod.
# Not used by LinuxCNC directly, used in the HAL file.
EMCMOT = motmod

# Number of seconds to wait for the motion module to
# confirm receipt of messages from the task module.
COMM_TIMEOUT = 1.0

# Servo thread period
# Not used by LinuxCNC directly, used in the HAL file.
SERVO_PERIOD = 1000000


[HAL]
# Hardware Abstraction Layer (HAL) configuration

# Adds HAL user interface pins.
HALUI = halui

# HAL file to execute when starting LinuxCNC.
# Can be specified multiple times.
HALFILE = mesa_7i96s_7i77_xy.hal

# HAL file to execute after loading the graphical interface.
POSTGUI_HALFILE = postgui.hal

# HAL file to execute when closing LinuxCNC.
SHUTDOWN = shutdown.hal


[HALUI]
# HAL User Interface

# MDI command. Can be specified multiple times.
# To execute it use the halui.mdi-command-NN pin,
# where NN is the command number.
# MDI_COMMAND = G1 X0 Y0 Z0


[KINS]
# Kinematics

# Number of joints (motors).
JOINTS = 2

# Kinematics module
# Not used by LinuxCNC directly, used in the HAL file.
KINEMATICS = trivkins coordinates=XY


[APPLICATIONS]
# Additional applications

# Application to run. Can be specified multiple times.
APP=halscope 50000


[TRAJ]
# Trajectory planner configuration

# Controlled axes. Possible values: X, Y, Z, A, B, C, U, V, W.
# An axis can be specified more than once, e.g., XXYZ.
COORDINATES =  XY

# Units for linear axes.
LINEAR_UNITS = mm

# Units for rotary axes.
ANGULAR_UNITS = degree

# Maximum linear velocity, in units per second.
MAX_LINEAR_VELOCITY = 12.00

# Maximum linear acceleration, in units per second^2.
MAX_LINEAR_ACCELERATION = 20.0


[EMCIO]
# Input/Output (I/O) controller configuration

# Input/output controller module.
EMCIO = io

# Period at which EMCIO will be executed.
CYCLE_TIME = 0.100


[AXIS_X]
# X-axis configuration

# Maximum axis velocity, in units per second.
MAX_VELOCITY = 12.0

# Maximum axis acceleration, in units per second^2.
MAX_ACCELERATION = 20.0

# Minimum limit for the axis, in machine units.
MIN_LIMIT = -5

# Maximum limit for the axis, in machine units.
MAX_LIMIT = 205.0


[JOINT_0]
# First linear motor configuration (X-axis)

# Motor type, LINEAR or ANGULAR.
TYPE = LINEAR

# Maximum following error, in machine units.
FERROR = 1.0

# Maximum following error at slow speeds.
MIN_FERROR = 0.2

# Maximum motor velocity, in units per second.
MAX_VELOCITY = 12.0

# Maximum motor acceleration, in units per second^2.
MAX_ACCELERATION = 20.0

# Minimum motor limit, in machine units.
MIN_LIMIT = -5

# Maximum motor limit, in machine units.
MAX_LIMIT = 205.0

# Position to which the joint will move upon completion
# of the homing process.
HOME = 0

# Used to define the homing order.
HOME_SEQUENCE = 0

# Position of the home switch, in machine units.
HOME_OFFSET = -10

# Initial homing search velocity, in units per second.
HOME_SEARCH_VEL = -1

# Final homing search velocity, in units per second.
HOME_LATCH_VEL = -0.25

# Final homing velocity, in units per second.
HOME_FINAL_VEL = 2

# Ignore limit switches during homing.
# = YES if the same switch is used for limits and homing.
HOME_IGNORE_LIMITS = YES

# The switch is shared with another joint.
HOME_IS_SHARED = 0

# Use the encoder's index pulse for homing.
HOME_USE_INDEX = NO

# ---------------------------------------------------
# Custom configurations for the HAL file.
# ---------------------------------------------------

# *** Step generation configuration ***

# Minimum duration of the stable direction signal before
# starting a step, in nanoseconds.
DIRSETUP   = 10000

# Minimum duration of the direction signal after finishing
# a step, in nanoseconds.
DIRHOLD    = 10000

# Duration of the step signal, in nanoseconds.
STEPLEN    = 2500

# Minimum interval between step signals, in nanoseconds.
STEPSPACE  = 2500

# Step scale. position = steps / STEP_SCALE.
# To move the axis 1mm/rev with a motor with 1.8 degree step and
# 1/32 microstepping mode, STEP_SCALE = steps / position = (32*360/1.8)/1 = 6400
STEP_SCALE = 6400

# Maximum velocity, in position units per second.
STEPGEN_MAXVEL = 17

# Maximum acceleration, in position units per second^2.
STEPGEN_MAXACCEL = 62.5

# Note: It is recommended that STEPGEN_MAXVEL and STEPGEN_MAXACCEL be
# between 1% and 25% larger than MAX_VELOCITY and MAX_ACCELERATION.


# *** Encoder configuration ***

# Encoder scale. position = counts / ENCODER_SCALE.
# To get 1mm/rev with a 1000 ppr (4000 cpr) encoder,
# ENCODER_SCALE = counts / position = 4000 / 1 = 4000
ENCODER_SCALE = 4000.0


# *** PID controller configuration ***

P = 50.0
I = 20.0
D = 0.0
FF0 = 0.0
FF1 = 1.0
FF2 = 0.025
BIAS = 0.0
DEADBAND = 0.0
MAX_OUTPUT = 0.0


[AXIS_Y]
# Y-axis configuration

# Maximum axis velocity, in units per second.
MAX_VELOCITY = 12.0

# Maximum axis acceleration, in units per second^2.
MAX_ACCELERATION = 20.0

# Minimum limit for the axis, in machine units.
MIN_LIMIT = -5

# Maximum limit for the axis, in machine units.
MAX_LIMIT = 205.0


[JOINT_1]
# Second linear motor configuration (Y-axis)

# Motor type, LINEAR or ANGULAR.
TYPE = LINEAR

# Maximum following error, in machine units.
FERROR = 1

# Maximum following error at slow speeds.
MIN_FERROR = 0.2

# Maximum motor velocity, in units per second.
MAX_VELOCITY = 12.0

# Maximum motor acceleration, in units per second^2.
MAX_ACCELERATION = 20.0

# Minimum motor limit, in machine units.
MIN_LIMIT = -5

# Maximum motor limit, in machine units.
MAX_LIMIT = 205.0

# Position to which the joint will move upon completion
# of the homing process.
HOME = 0

# Used to define the homing order.
HOME_SEQUENCE = 1

# Position of the home switch, in machine units.
HOME_OFFSET = -10

# Initial homing search velocity, in units per second.
HOME_SEARCH_VEL = -1

# Final homing search velocity, in units per second.
HOME_LATCH_VEL = -0.25

# Final homing velocity, in units per second.
HOME_FINAL_VEL = 2

# Ignore limit switches during homing.
# = YES if the same switch is used for limits and homing.
HOME_IGNORE_LIMITS = YES

# The switch is shared with another joint.
HOME_IS_SHARED = 0

# Use the encoder's index pulse for homing.
HOME_USE_INDEX = NO

# ---------------------------------------------------
# Custom configurations for the HAL file.
# ---------------------------------------------------

# *** Analog output configuration for +-10V ***

# Maximum speed in units per second.
ANALOGOUT_MAXLIM = 50

# Minimum speed in units per second.
ANALOGOUT_MINLIM = -50

# Analog output scale. Vout = 10 * vel. / ANALOGOUT_SCALE.
# Maximum velocity in units per second that the motor can reach.
# For a maximum velocity of X rpm, with an encoder of Y ppr (4*Y cpr),
# ANALOGOUT_SCALE = X / 60 * ENCODER_SCALE / (4*Y).
# For 3000 rpm, ANALOGOUT_SCALE = 3000 / 60 * 2048 / 2048 = 50
ANALOGOUT_SCALE = 50


# *** Encoder configuration ***

# Encoder scale. position = counts / ENCODER_SCALE.
# To get 1mm/rev with a 512 ppr (2048 cpr) encoder,
# ENCODER_SCALE = counts / position = 2048 / 1 = 2048
ENCODER_SCALE = 2048.0
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

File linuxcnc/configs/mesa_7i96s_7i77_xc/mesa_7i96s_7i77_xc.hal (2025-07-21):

loadrt [KINS]KINEMATICS
loadrt [EMCMOT]EMCMOT servo_period_nsec=[EMCMOT]SERVO_PERIOD num_joints=[KINS]JOINTS

loadrt hostmot2
loadrt hm2_eth board_ip="10.68.33.122" config="num_encoders=2 num_pwmgens=0 num_stepgens=1"
loadrt classicladder_rt
loadrt pid names=pid.x,pid.c
loadrt estop_latch
loadrt oneshot
loadrt logic names=logic.fault personality=0x205

# set 7i96s watchdog timeout
setp hm2_7i96s.0.watchdog.timeout_ns 5000000

# configure hostmod2 dpll (phased locked loop)
setp hm2_7i96s.0.dpll.01.timer-us -100
setp hm2_7i96s.0.stepgen.timer-number 1
setp hm2_7i96s.0.encoder.timer-number 1

# configure oneshot
setp oneshot.0.width 0.1

# ddt module for calculating acceleration
loadrt ddt count=1
addf ddt.0 servo-thread
net Y-vel joint.0.vel-cmd => ddt.0.in

# add functions to servo thread
addf motion-command-handler servo-thread
addf motion-controller servo-thread
addf pid.x.do-pid-calcs servo-thread
addf pid.c.do-pid-calcs servo-thread
addf hm2_7i96s.0.read servo-thread
addf hm2_7i96s.0.write servo-thread
addf classicladder.0.refresh servo-thread
addf estop-latch.0 servo-thread
addf oneshot.0 servo-thread
addf logic.fault servo-thread

# load classic ladder project
loadusr classicladder myladder.clp --nogui


#********************
# AXIS X --- JOINT 0
#********************

# --- PID parameters ---

setp pid.x.Pgain     [JOINT_0]P
setp pid.x.Igain     [JOINT_0]I
setp pid.x.Dgain     [JOINT_0]D
setp pid.x.bias      [JOINT_0]BIAS
setp pid.x.FF0       [JOINT_0]FF0
setp pid.x.FF1       [JOINT_0]FF1
setp pid.x.FF2       [JOINT_0]FF2
setp pid.x.deadband  [JOINT_0]DEADBAND
setp pid.x.maxoutput [JOINT_0]MAX_OUTPUT
setp pid.x.error-previous-target true

# This setting is to limit bogus stepgen
# velocity corrections caused by position
# feedback sample time jitter.
setp pid.x.maxerror 1


# --- Analog output parameters ---

setp hm2_7i96s.0.7i77.0.1.analogout0-maxlim [JOINT_0]ANALOGOUT_MAXLIM
setp hm2_7i96s.0.7i77.0.1.analogout0-minlim [JOINT_0]ANALOGOUT_MINLIM
setp hm2_7i96s.0.7i77.0.1.analogout0-scalemax [JOINT_0]ANALOGOUT_SCALE


# --- Encoder parameters ---

setp hm2_7i96s.0.encoder.01.counter-mode 0
setp hm2_7i96s.0.encoder.01.filter 1
setp hm2_7i96s.0.encoder.01.scale [JOINT_0]ENCODER_SCALE


# --- Connect pid / analog / motion signals ----

net pid-x-index-enable => pid.x.index-enable

net pid-x-output <= pid.x.output
net pid-x-output => hm2_7i96s.0.7i77.0.1.analogout0

net pid-x-enable <= joint.0.amp-enable-out
net pid-x-enable => pid.x.enable
net pid-x-enable => hm2_7i96s.0.7i77.0.1.analogena 

net pid-x-pos-cmd <= joint.0.motor-pos-cmd
net pid-x-pos-cmd => pid.x.command

net pid-x-pos-fb <= hm2_7i96s.0.encoder.01.position
net pid-x-pos-fb => pid.x.feedback
net pid-x-pos-fb => joint.0.motor-pos-fb


# --- Setup home / limit switch signals ---

net y-sw <= hm2_7i96s.0.gpio.001.in
net y-sw => joint.0.home-sw-in
net y-sw => joint.0.neg-lim-sw-in


#********************
# AXIS C --- JOINT 1
#********************

# --- PID parameters ---

setp pid.c.Pgain     [JOINT_1]P
setp pid.c.Igain     [JOINT_1]I
setp pid.c.Dgain     [JOINT_1]D
setp pid.c.bias      [JOINT_1]BIAS
setp pid.c.FF0       [JOINT_1]FF0
setp pid.c.FF1       [JOINT_1]FF1
setp pid.c.FF2       [JOINT_1]FF2
setp pid.c.deadband  [JOINT_1]DEADBAND
setp pid.c.maxoutput [JOINT_1]MAX_OUTPUT
setp pid.c.error-previous-target true

# This setting is to limit bogus stepgen
# velocity corrections caused by position
# feedback sample time jitter.
setp pid.c.maxerror 1


# --- Step Gen parameters ---

setp hm2_7i96s.0.stepgen.00.control-type   1  # Velocity control
setp hm2_7i96s.0.stepgen.00.step_type      0  # Step/dir
# setp hm2_7i96s.0.stepgen.00.direction.invert_output 1 # Invert direction signal
setp hm2_7i96s.0.stepgen.00.dirsetup       [JOINT_1]DIRSETUP
setp hm2_7i96s.0.stepgen.00.dirhold        [JOINT_1]DIRHOLD
setp hm2_7i96s.0.stepgen.00.steplen        [JOINT_1]STEPLEN
setp hm2_7i96s.0.stepgen.00.stepspace      [JOINT_1]STEPSPACE
setp hm2_7i96s.0.stepgen.00.position-scale [JOINT_1]STEP_SCALE
setp hm2_7i96s.0.stepgen.00.maxaccel       [JOINT_1]STEPGEN_MAXACCEL
setp hm2_7i96s.0.stepgen.00.maxvel         [JOINT_1]STEPGEN_MAXVEL


# --- Encoder parameters ---

setp hm2_7i96s.0.encoder.00.counter-mode 0
setp hm2_7i96s.0.encoder.00.filter 1
setp hm2_7i96s.0.encoder.00.scale [JOINT_1]ENCODER_SCALE


# --- Connect pid / stepgen / motion signals ----

net pid-c-index-enable => pid.c.index-enable

net pid-c-output <= pid.c.output
net pid-c-output => hm2_7i96s.0.stepgen.00.velocity-cmd

net pid-c-enable <= joint.1.amp-enable-out
net pid-c-enable => pid.c.enable
net pid-c-enable => hm2_7i96s.0.stepgen.00.enable

net pid-c-pos-cmd <= joint.1.motor-pos-cmd
net pid-c-pos-cmd => pid.c.command

# net pid-c-pos-fb <= hm2_7i96s.0.stepgen.00.position-fb
net pid-c-pos-fb <= hm2_7i96s.0.encoder.00.position
net pid-c-pos-fb => pid.c.feedback
net pid-c-pos-fb => joint.1.motor-pos-fb


# --- Setup home / limit switch signals ---

net c-index-enable <=> hm2_7i96s.0.encoder.00.index-enable
net c-index-enable <=> joint.1.index-enable

# net x-sw <= hm2_7i96s.0.gpio.000.in
# net x-sw => joint.1.home-sw-in
# net x-sw => joint.1.neg-lim-sw-in


#***********************
# Miscellaneous signals
#***********************

# --- Controller alert/error signals ---
net X-alert <= hm2_7i96s.0.7i77.0.0.input-08
net X-error <= hm2_7i96s.0.7i77.0.0.input-09

net Y-alert <= hm2_7i96s.0.7i77.0.0.input-01
net Y-error <= hm2_7i96s.0.7i77.0.0.input-02


# --- Fault signal ---
# We set the fault signal if any controller signals an error or alert
# or if the user presses the estop button

net remote-estop <= hm2_7i96s.0.7i77.0.0.input-13

net X-alert => logic.fault.in-00
net X-error => logic.fault.in-01

net Y-alert => logic.fault.in-02
net Y-error => logic.fault.in-03

net remote-estop => logic.fault.in-04


# --- ESTOP ---
net user-enable <= iocontrol.0.user-enable-out
net user-enable => estop-latch.0.ok-in

net user-request-enable <= iocontrol.0.user-request-enable
net user-request-enable => estop-latch.0.reset

net fault <= logic.fault.or
net fault => estop-latch.0.fault-in

net emc-enable <= estop-latch.0.ok-out
net emc-enable => iocontrol.0.emc-enable-in


# --- Enable joints ---
net machine-on <= halui.machine.is-on
net machine-on => hm2_7i96s.0.7i77.0.0.output-00


# --- Output pulse for starting brushless rotation program ---
net brushless-ready <= hm2_7i96s.0.7i77.0.0.input-00
net brushless-ready => oneshot.0.in

net start-brushless <= oneshot.0.out
net start-brushless => hm2_7i96s.0.7i77.0.0.output-01


# --- LED panel lights ---
net machine-estop <= halui.estop.is-activated

net machine-estop => classicladder.0.in-00
net remote-estop => classicladder.0.in-01 
net machine-on => classicladder.0.in-02

net X-error => classicladder.0.in-03
net X-alert => classicladder.0.in-08

net Y-error => classicladder.0.in-05
net Y-alert => classicladder.0.in-10

net led-red <= classicladder.0.out-00
net led-red => hm2_7i96s.0.7i77.0.0.output-02

net led-yellow <= classicladder.0.out-01
net led-yellow => hm2_7i96s.0.7i77.0.0.output-03

net led-green <= classicladder.0.out-02
net led-green => hm2_7i96s.0.7i77.0.0.output-04


#******
# TEST 
#******

# loop position commands back to motion module feedback
# net Xpos <= joint.1.motor-pos-cmd
# net Xpos => joint.1.motor-pos-fb

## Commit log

2025-07-21 Translated documentation chapter 3 LinuxCNC config file comments
    [mesa_7i96s_7i77_xy.hal, mesa_7i96s_7i77_xy.ini]
2025-07-21 Translated and reviewed comments in LinuxCNC configuration files
    [mesa_7i96s_7i77_xc.hal, mesa_7i96s_7i77_xc.ini, mesa_7i96s_7i77_xx.ini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]

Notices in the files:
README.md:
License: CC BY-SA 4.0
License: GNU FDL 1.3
